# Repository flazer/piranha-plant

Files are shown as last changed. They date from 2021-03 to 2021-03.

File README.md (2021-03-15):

# Remote controlled "Mario piranha plant"

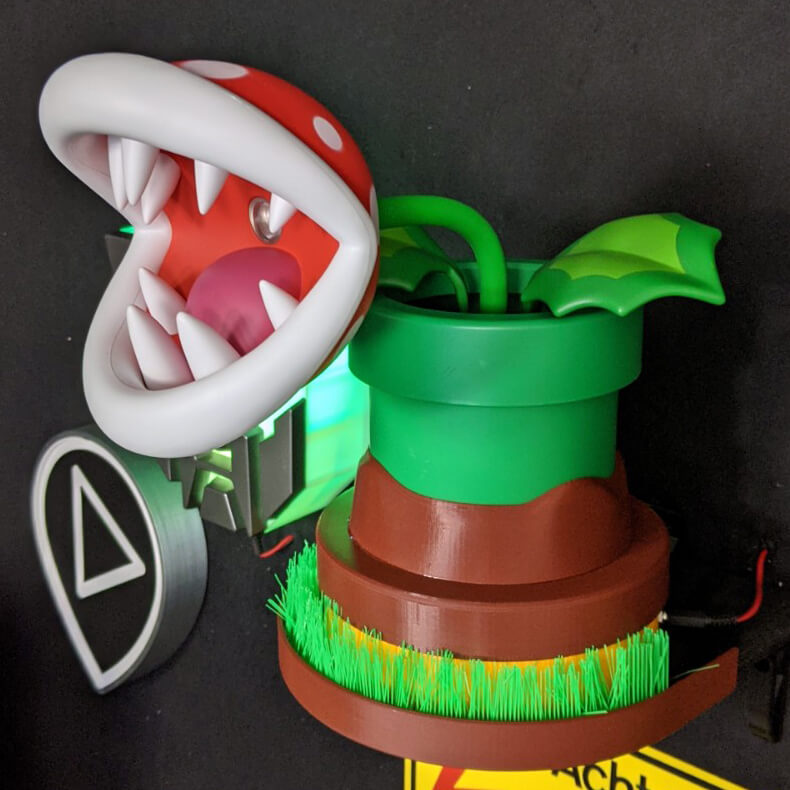
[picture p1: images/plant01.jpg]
Mario piranha plant


## Introduction
This project was realized while streaming live at [https://www.twitch.tv/chrisfigge](https://www.twitch.tv/chrisfigge).
I got this piranha plant as a christmas-gift but I think it's much cooler to use it as a remote controlled gadget while streaming.
So I wrote a lot of code, printed a lot of stuff and did this electronic-thingie.
But this time with a lot of help from the mighty community.
[0FR0](https://github.com/0FR0) tried to teach me KiCad and developed my first PCB ever.
Many, many thanks, dude! Awesome job!

So you'll find everything you need to build your own remote controlled plant in here:

- BOM (everything you've to buy)
- STL files (everything to print)
- images (everything you need to watch)
- code (everything to controll your plant via wifi)
- schematics (everything to build your own circuit)

## BOM
- 1x Wemos D1 mini: [https://amzn.to/389YZPE](https://amzn.to/389YZPE) *
- 1x Nema17 Pancake: [https://amzn.to/3bYEyGN](https://amzn.to/3bYEyGN) *
- 2x 10kOhm Resistors: [https://amzn.to/3sRnLwe](https://amzn.to/3sRnLwe) *
- 1x TMC2208 (Stepperdriver): [https://amzn.to/2PzTYd1](https://amzn.to/2PzTYd1) *
- 1x IRFZ44N (Mosfet): [https://amzn.to/3kILgEA](https://amzn.to/3kILgEA) *
- 1x LM2596 (Stepdown module): [https://amzn.to/38aoLn4](https://amzn.to/38aoLn4) *
- 1x Microswitch [https://amzn.to/3rUtHEC](https://amzn.to/3rUtHEC) *
- 1x DC-Plug [https://amzn.to/3rSaIKy](https://amzn.to/3rSaIKy) *

Links marked with an asterisk (*) are affiliates. This means if you order these items via amazon, i'll get a very small piece of this (financial) cake. You'll not pay more (not even 1 cent. literally nothing). And I can reinvest the money for new ideas and projects. From the community for the community. :)

## PCB
The pcb shown in "images" are an old previous version and differs from the current state. But works exactly the same.

## Enclosure  
If you want to print the case I've used please take a look into the "stls"-folder.  
The files are named as what they are used for.
To get a better understanding, please watch the images, stored in the "images"-folder.

## Assembly
To assemble the 3d printed parts. You will need some glue, to glue the inlay parts.
Because I'm not very good in get parts in correct position, I've printed a centering guide.
Just place the guide onto the platform and glue the "hill" nearly perfectly centered onto the baseplate. Remove the guide afterwards.

## Twitch

If you are interested in what I'm doing, just have a look at twitch:
[https://www.twitch.tv/chrisfigge](https://www.twitch.tv/chrisfigge)

## Tip
I am doing all this stuff in my freetime. And, oh boy, these projects take a lot of time. I swear.
If you want to support my work feel free to cheer some bits or giftsubs on my [Twitch channel](https://www.twitch.tv/chrisfigge) or you can always leave some tip via [paypal](https://paypal.me/flazer). Thanks a lot!

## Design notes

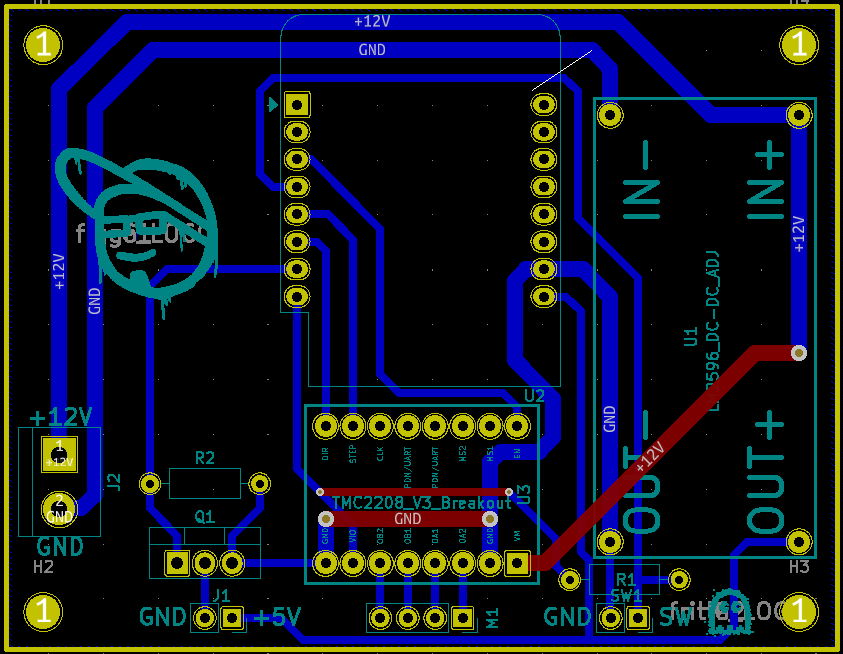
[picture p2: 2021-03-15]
schematics/layout.png

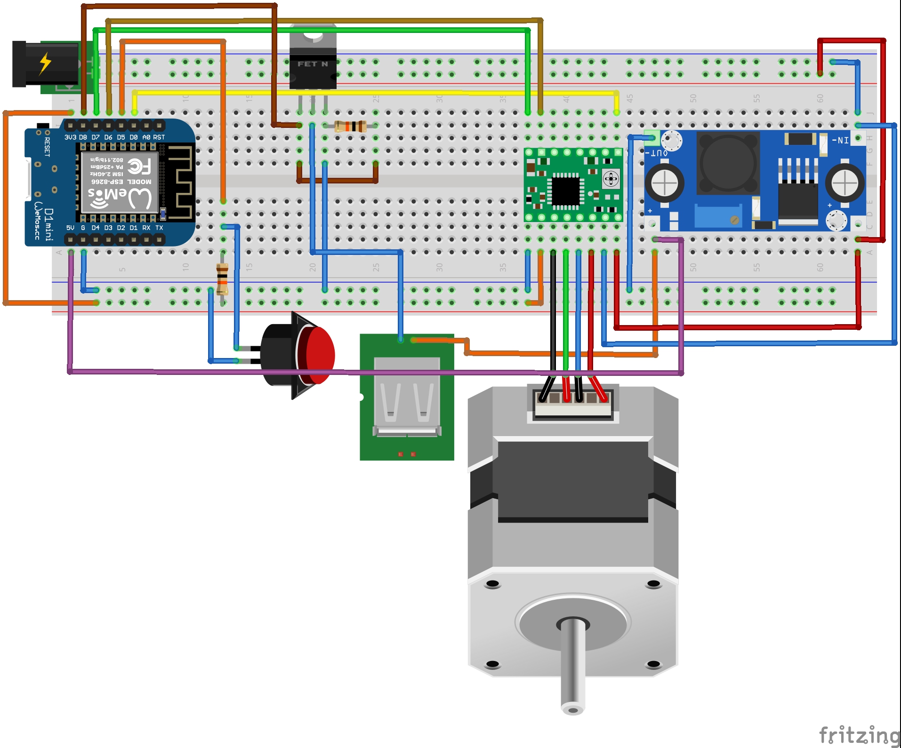
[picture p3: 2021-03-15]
schematics/fritzing/piranha-plant_Steckplatine.jpg

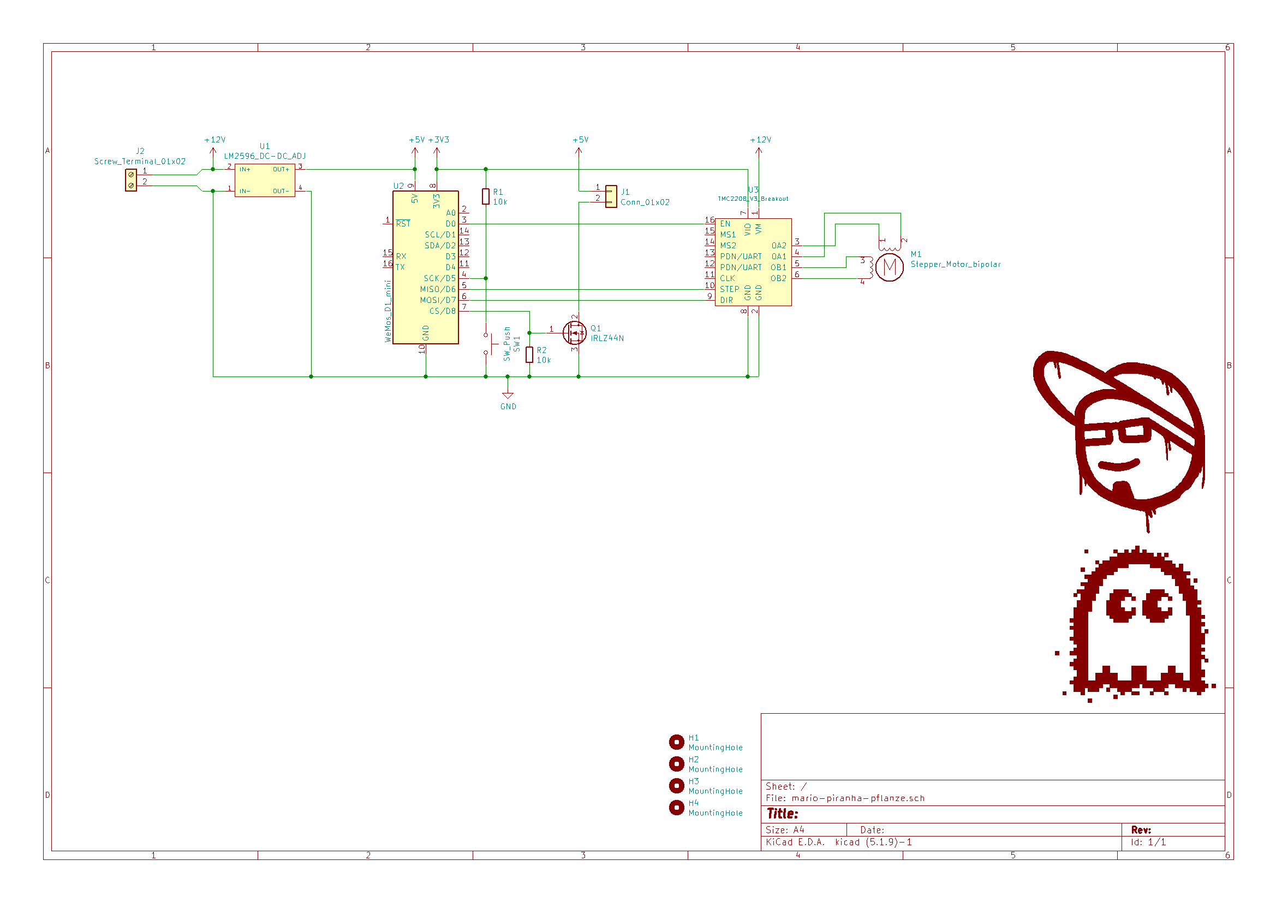
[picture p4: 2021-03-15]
schematics/scheme.png

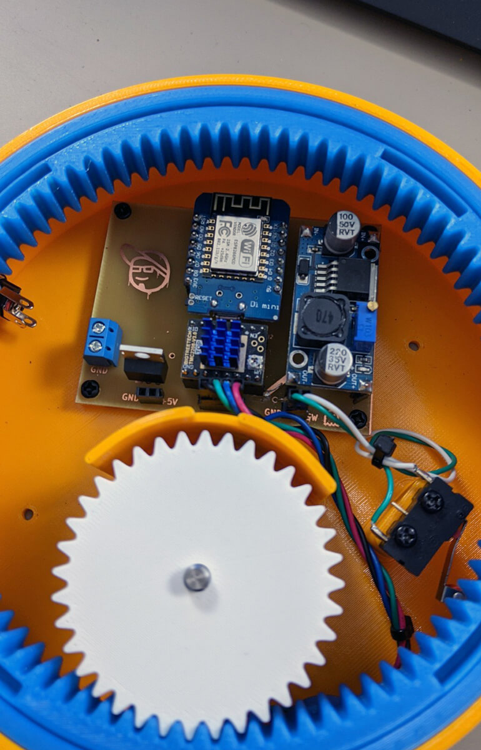
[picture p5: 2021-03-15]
images/plant05.jpg

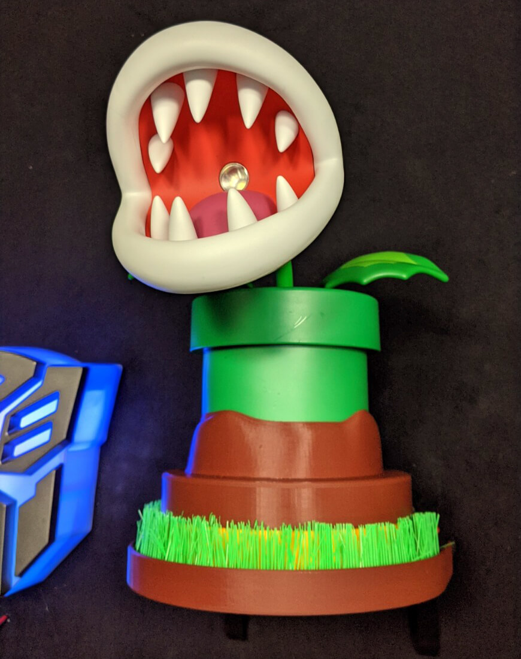
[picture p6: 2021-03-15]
images/plant02.jpg

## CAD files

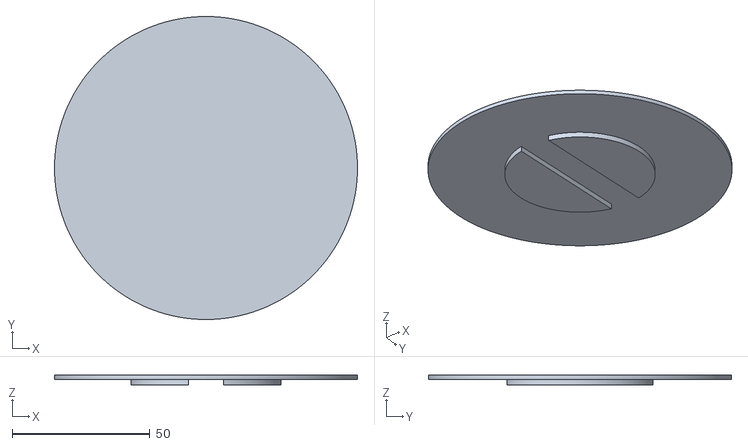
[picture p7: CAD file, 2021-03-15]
print/stl/centering-guide.stl
110.0 x 110.0 x 3.50

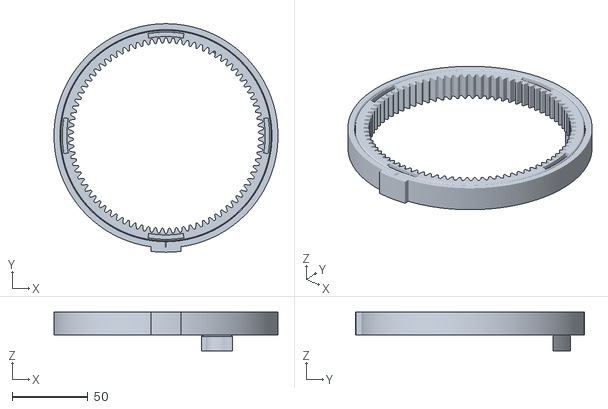
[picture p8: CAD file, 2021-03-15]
print/stl/gearring-84.stl
148.0 x 151.0 x 25.5

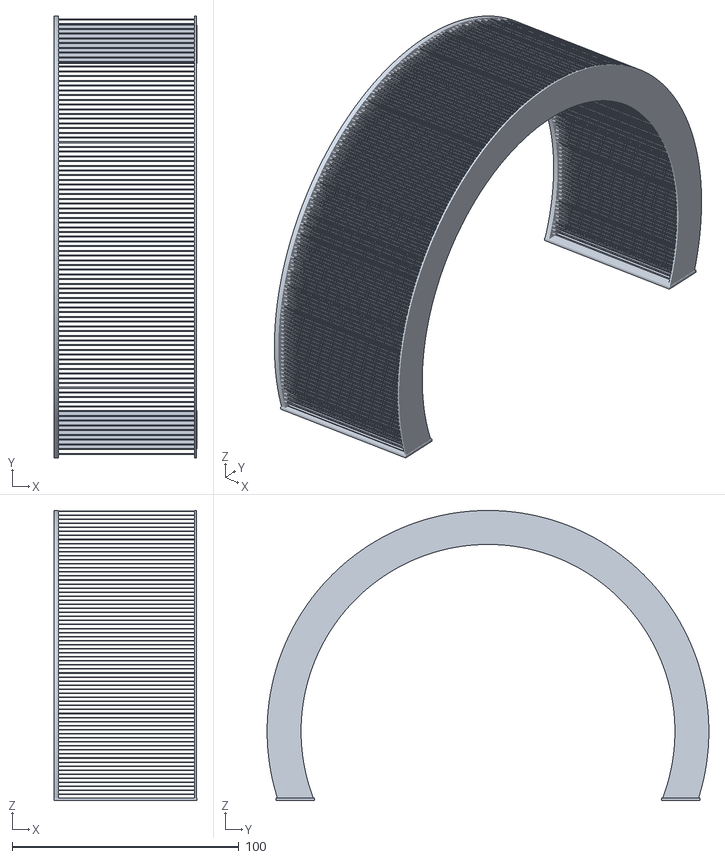
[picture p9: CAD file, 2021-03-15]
print/stl/grass.stl
63.0 x 195.0 x 128.0

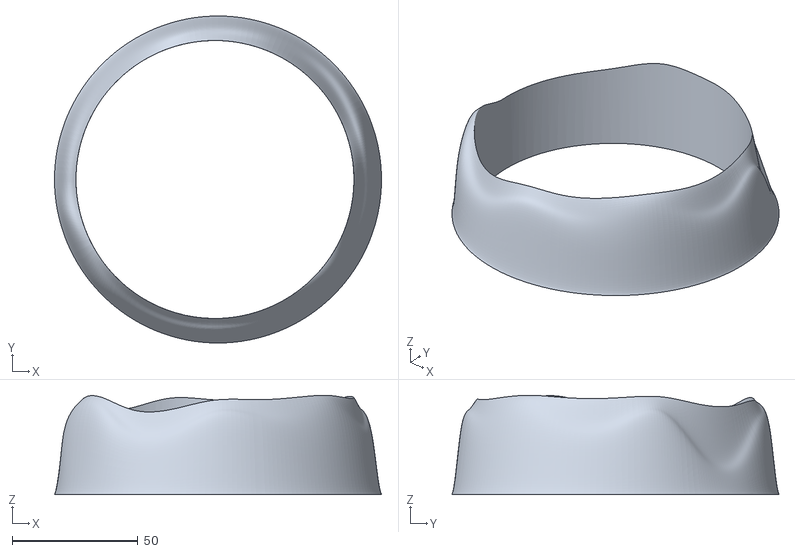
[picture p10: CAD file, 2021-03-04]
print/stl/hill.stl
130.0 x 130.0 x 39.5

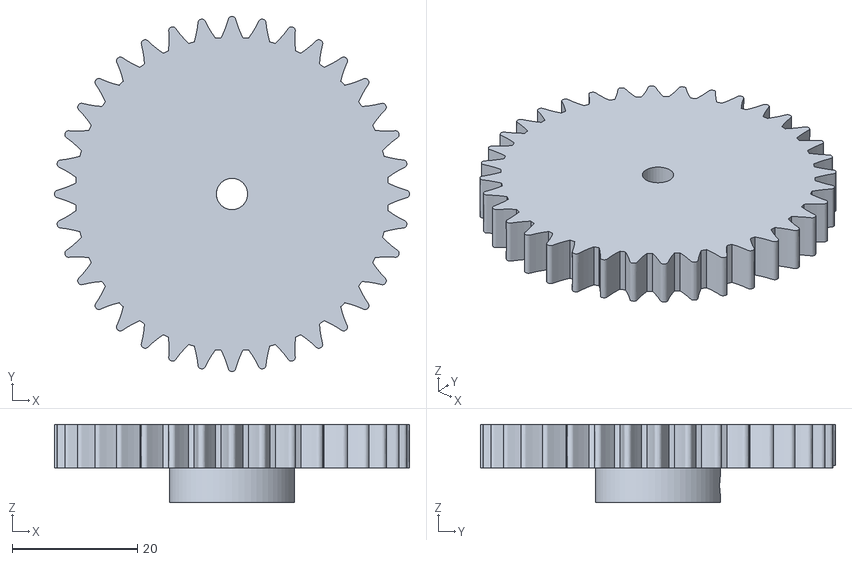
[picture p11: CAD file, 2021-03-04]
print/stl/gear-36.stl
56.7 x 56.7 x 12.5

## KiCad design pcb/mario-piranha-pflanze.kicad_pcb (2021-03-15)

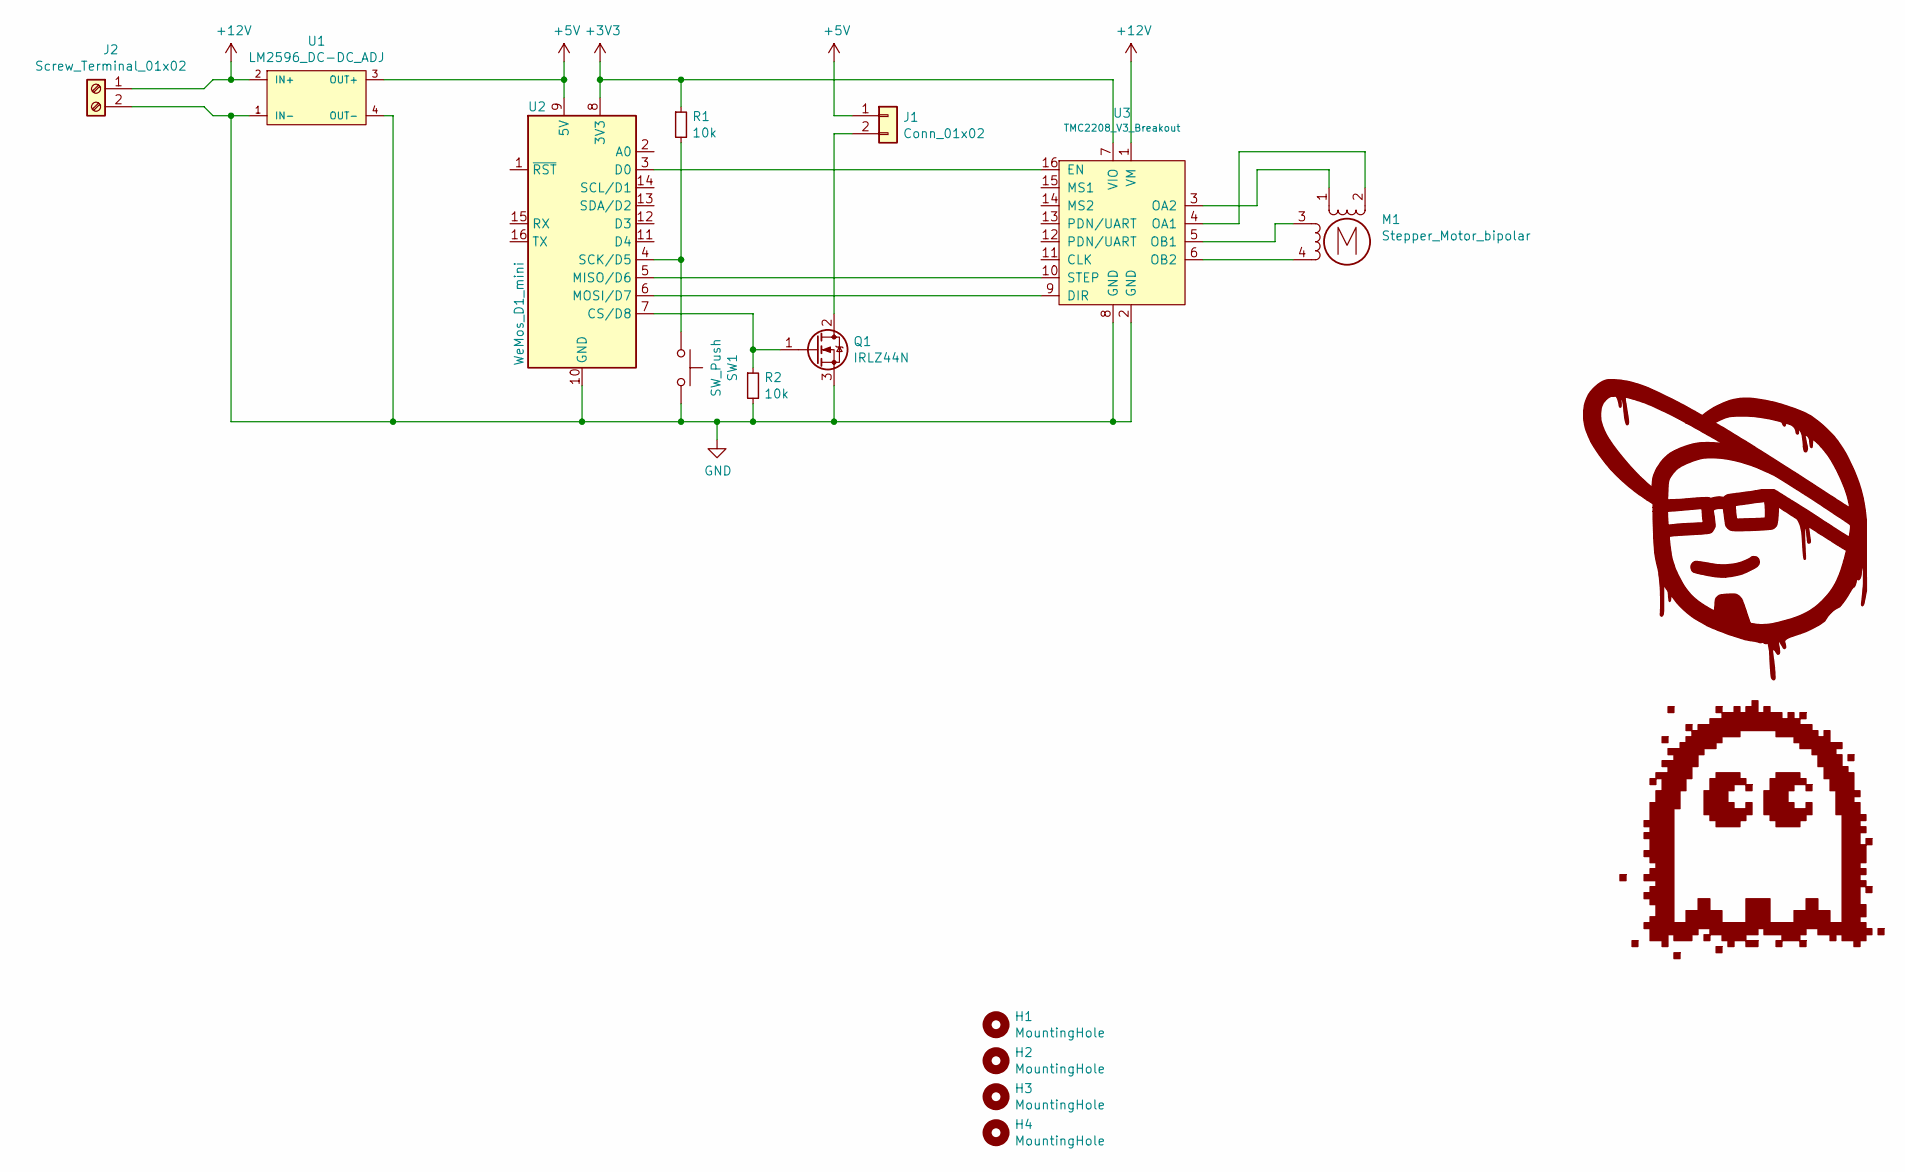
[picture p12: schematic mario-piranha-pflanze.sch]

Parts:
G1: figge_LOGO; figge_logo_15x15,9
G2: fritte_LOGO; fritte_LOGO_5x5
H1, H2, H3, H4: MountingHole; MountingHole_3.2mm_M3
J1: Conn_01x02; PinSocket_1x02_P2.54mm_Vertical
J2: Screw_Terminal_01x02; TerminalBlock_bornier-2_P5.08mm
M1: Stepper_Motor_bipolar; PinSocket_1x04_P2.54mm_Vertical
Q1: IRLZ44N; TO-220-3_Vertical
R1, R2: 10k; R_Axial_DIN0207_L6.3mm_D2.5mm_P10.16mm_Horizontal
SW1: SW_Push; PinSocket_1x02_P2.54mm_Vertical
U1: LM2596_DC-DC_ADJ; LM2596_DC-DC
U2: WeMos_D1_mini; WEMOS_D1_mini_light
U3: TMC2208_V3_Breakout

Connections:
+3V3: R1.1, U2.8 (3V3), U3.7 (VIO)
+5V: J1.1, U1.3 (OUT+), U2.9 (5V)
+12V: J2.1, U1.2 (IN+), U3.1 (VM)
GND: J2.2, Q1.3 (S), R2.2, SW1.2, U1.1 (IN-), U1.4 (OUT-), U2.10 (GND), U3.2 (GND), U3.8 (GND)
unnamed: J1.2, Q1.2 (D)
unnamed: M1.1, U3.3 (OA2)
unnamed: M1.2 (-), U3.4 (OA1)
unnamed: M1.3, U3.5 (OB1)
unnamed: M1.4, U3.6 (OB2)
unnamed: Q1.1 (G), R2.1, U2.7 (CS/D8)
unnamed: R1.2, SW1.1, U2.4 (SCK/D5)
unnamed: U2.3 (D0), U3.16 (EN)
unnamed: U2.5 (MISO/D6), U3.10 (STEP)
unnamed: U2.6 (MOSI/D7), U3.9 (DIR)

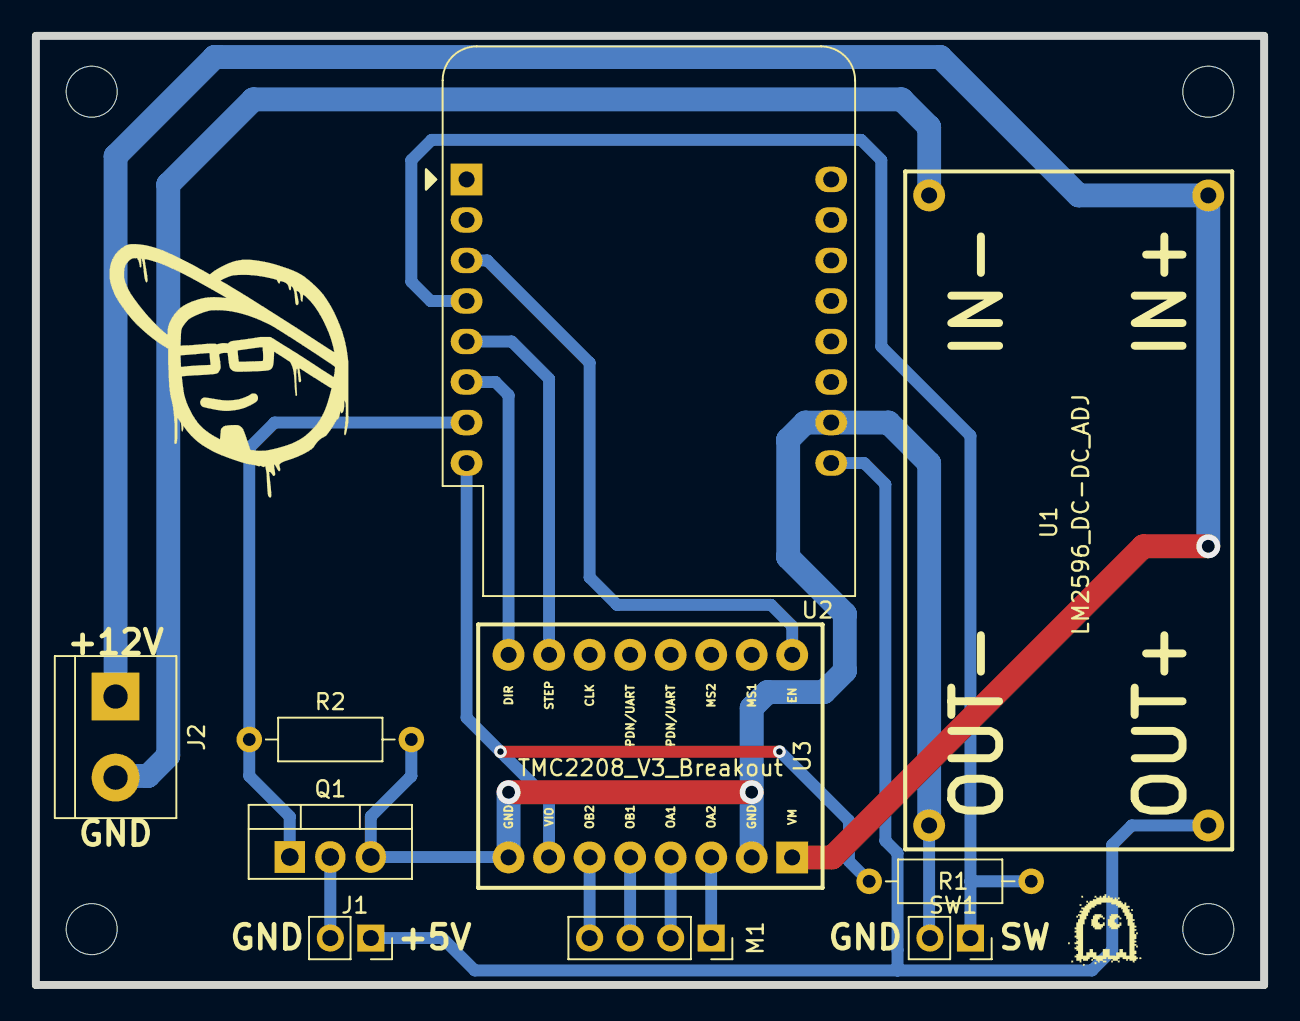
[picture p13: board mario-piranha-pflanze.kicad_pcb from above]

Board: 2 copper layers, 77.0 x 59.5 mm, 16 parts (0 on the bottom side), 14 nets.

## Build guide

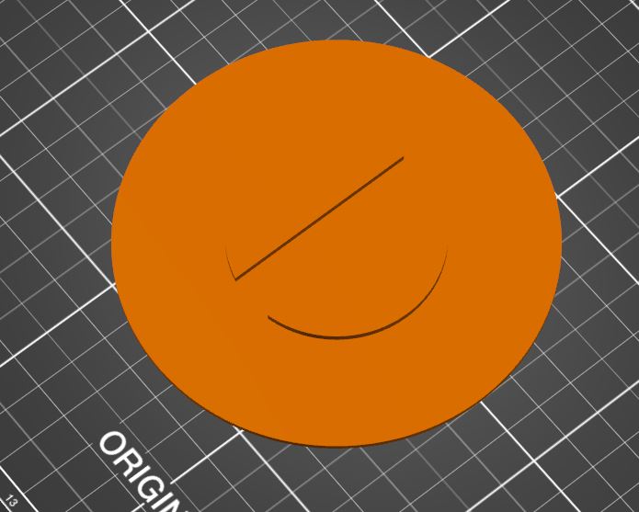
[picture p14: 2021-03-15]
print/images/centering-guide.JPG

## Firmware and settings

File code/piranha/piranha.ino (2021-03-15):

#include <ESP8266WiFi.h>
#include <ESP8266WiFiMulti.h>
#include <ESP8266HTTPClient.h>
#include <ESP8266WebServer.h>
#include <ESP8266mDNS.h>
#include <ESP8266Ping.h> //https://github.com/dancol90/ESP8266Ping
#include <Ticker.h>
#include <AccelStepper.h> //http://www.airspayce.com/mikem/arduino/AccelStepper/

#include "credentials.h"
#include "settings.h"
#include "OTA.h"

ESP8266WiFiMulti  WiFiMulti;
ESP8266WebServer  server(80);
Ticker            ticker;
AccelStepper      stepper(AccelStepper::DRIVER, STEPPER_STEP, STEPPER_DIR);
 
void setup() {
  Serial.begin(115200);
  delay(300);

  Serial.println();
  Serial.println("Setting inputs/outputs...");
  Serial.println();
  
  pinMode(BTN, INPUT);
  pinMode(LED, OUTPUT);
  pinMode(STEPPER_STEP, OUTPUT);
  pinMode(STEPPER_DIR, OUTPUT);
  pinMode(STEPPER_ENABLE, OUTPUT);
   
  digitalWrite(STEPPER_STEP, LOW);
  digitalWrite(STEPPER_DIR, LOW);
  digitalWrite(LED, LOW);
  enableMotor(false);
  
  Serial.println();
  Serial.println("Starting ticker...");
  Serial.println();
  ticker.attach(1, loopCount);

  Serial.println();
  Serial.println("Initializing stepper...");
  Serial.println();
  stepper.setAcceleration(80);
  stepper.setMaxSpeed(maxMotorSpeed);
  
  Serial.println("");
  startWIFI();
  handleOTASetup();
  startWebserver();

  Serial.println();
  Serial.println("Homing");
  homingMode = true;
  Serial.println();
}


/**
 * Wrapper for more ease moving 
 * the motor
 */
void moveDeg(int deg) {
  // 360° = 466 * 8 = 3728 steps
  int steps = 466 * 8 / 360;
  steps = steps * deg;
  Serial.println(steps);
  stepper.move(steps);
}


/**
 * Homing the whole platform
 * Handling when state is in "homing"-mode.
 */
void homePlatform() {
  enableMotor(true);

  switch(homingModeStep) {
    case 0:
      digitalWrite(LED, HIGH);
      stepper.setSpeed(maxMotorSpeed);
      moveDeg(10);
      homingModeStep++;
      break;

    case 1:
      if(!stepper.isRunning()) {
        digitalWrite(LED, LOW);
        moveDeg(-180);
        homingModeStep++;
      }
      break;

    case 2:
      if(!digitalRead(BTN)) {
        stepper.setAcceleration(avgAccSpeed * 2);
        stepper.stop();
        homingModeStep++;
      }
      break;

    case 3:
      if(!stepper.isRunning()) {
        stepper.setAcceleration(avgAccSpeed);
        digitalWrite(LED, HIGH);
        moveDeg(60);
        homingModeStep++;
      }
    break;

    case 4:
      if(!stepper.isRunning()) {
        digitalWrite(LED, LOW);
        stepper.disableOutputs();
        enableMotor(false);
        homingModeStep = 99;
        homingMode = false;
        Serial.println("Successfully homed!");
      }
    break;
  }
}


/**
 * Playing moving pattern
 * Handling when state is in "patternActive"-mode.
 */
void playPattern() {
  enableMotor(true);

  switch(patternStep) {
    case 0:
      moveDeg(60);
      patternStep++;
      break;

    case 1:
      if(!stepper.isRunning()) {
        moveDeg(-125);
        patternStep++;
      }
      break;

    case 2:
      if(!digitalRead(BTN)) {
        stepper.setAcceleration(avgAccSpeed * 2);
        stepper.stop();
        patternStep++;
      }
      break;

    case 3:
      if(!stepper.isRunning()) {
        stepper.setAcceleration(avgAccSpeed);
        moveDeg(120);
        if(patternLoop < patternRepeats) {
          patternLoop++;
          patternStep = 1;
        } else {
          patternStep++;
        }
      }
    break;

  case 4:
    if(!stepper.isRunning()) {
      moveDeg(-60);
      patternStep++;
    }
    break;

    case 5:
      if(!stepper.isRunning()) {
        stepper.disableOutputs();
        enableMotor(false);
        patternStep = 0;
        patternLoop = 0;
        patternLed = 0;
        ledActive = false;
        digitalWrite(LED, ledActive);
        patternActive = false;
        Serial.println("Successfully end pattern!");
      }
    break;
  }
}


/**
 * Switching led on/off if x ms passed
 */
void handleLed() {
  if(patternLed > 0 && lastHitMillis < millis() && millis() % 1000 == 0) {
    lastHitMillis = millis();
    ledActive = !ledActive;
    digitalWrite(LED, ledActive);
  }
}


/**
   Handles pinging (send alive)
   to server
*/
void handlePing() {
  if (pingCnt > handlePingSecs) {
    Serial.println("Start pinging.");
    bool result = Ping.ping("www.google.com");

    if (!result) {
      Serial.println("Ping failed!");
    }

    Serial.println("[HTTP] end ping-pong.");
    Serial.println("---");
    pingCnt = 0;
  }
}


/**
 * Preparing movePattern by parsing and setting 
 * all params given by request
 */
void startMovePattern(uint8_t speed, uint8_t repeats, uint8_t led) {
  server.send(200, "text/plain", "Start movement.");
  patternActive = true;

  patternSpeed = patternSpeedFallback;
  if(speed > 0) patternSpeed = speed;
  if(speed > maxMotorSpeed) patternSpeed = maxMotorSpeed;

  patternRepeats = patternRepeatsFallback;
  if(repeats > 0) patternRepeats = repeats;
  
  patternLed = patternLedFallback;
  if(led > 0) patternLed = led;
  
  Serial.println("Start da movement");
}


/**
   Start webserver for handling
   incoming requests
*/
void startWebserver() {
  Serial.println("Starting HTTP-Server...");
  Serial.println("-- Registering routes.");
  server.on("/pattern", HTTP_GET, []() {
    String speed = server.arg("speed");
    String repeats = server.arg("repeats");
    String led = server.arg("led");
    startMovePattern(speed.toInt(), repeats.toInt(), led.toInt());
  });
  server.onNotFound(handleRequestNotFound);
  Serial.println("-- Launching server ...");
  server.begin();
  Serial.println("-- DONE.");
}


/**
   Start or reconnect the wifi
   by switching into an infinite loop
   as long as the connection is broken
*/
void startWIFI() {
  int loopcnt = 0;
  Serial.println("---");
  WiFi.mode(WIFI_STA);
  Serial.println("Connecting WIFI.");
  Serial.println("(Re)Connecting to Wifi-Network with following credentials:");
  Serial.print("SSID: ");
  //Serial.println(WifiCredentials[0].c_str());
  Serial.print("Key: ");
  //Serial.println(WifiCredentials[1].c_str());
  WiFi.hostname(espName);
  WiFiMulti.addAP(WifiCredentials[0].c_str(), WifiCredentials[1].c_str());

  while (WiFiMulti.run() != WL_CONNECTED) {
    loopcnt++;
    if(loopcnt < 10) {
      Serial.print(".");
    }
    delay(500);
  }

  Serial.println("");
  Serial.println("WiFi connected.");
  Serial.println("IP address:");
  Serial.println(WiFi.localIP().toString());
}


/**
   Tick, tick, tick
*/
void loopCount() {
  loopCnt++;
  pingCnt++;
}


/**
 * DA MAINLOOP
 */
void loop() {
   //(re)connect wifi if not connected
  if (WiFiMulti.run() != WL_CONNECTED) {
    delay(1);
    startWIFI();
    return;
  }

  stepper.run();

  if(homingMode) {
    homePlatform();
    return;  
  }

  if(patternActive) {
    playPattern();
    handleLed();
    return;
  }

  if(stepper.isRunning()) {
    return;
  }
  
  ArduinoOTA.handle();
  handlePing();
  server.handleClient();
   
}


/**
 * Wrapper for handling the motor more 
 * intuitively
 */
void enableMotor(boolean enable) {
  digitalWrite(STEPPER_ENABLE, !enable);
}


/**
   Unknown Route
   Send "teapot".
*/
void handleRequestNotFound() {
  server.send(418, "text/plain", "I'm a piranha-plant. Chhhrrapppp! Chhhrrapppp!");
}

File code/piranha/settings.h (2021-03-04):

#define BTN             D5 //Button
#define LED             D8 //LED
#define STEPPER_STEP    D6 //Step
#define STEPPER_DIR     D7 //Direction
#define STEPPER_ENABLE  D0 //Enable 

//Interval to ping server in seconds (to avoid losing wifi)
int handlePingSecs = 120;

int maxMotorSpeed = 500; //Maximum speed of motor
int avgAccSpeed   = 900; //Normal acceleration speed 

boolean patternLedFallback = 0; //Fallback if no led-option was send via request
uint8_t patternRepeatsFallback = 3; //Fallback if no repeat-option was send via request
uint8_t patternSpeedFallback = 500; //Fallback if no speed-option was send via request

//Hostname of your esp
const char* espName = "esp8266-studio-piranha-plant"; 

//Internal settings. 
//Don't change anything below (except you really know what you're doing).

int loopCnt = 0;
int pingCnt = 0;

boolean homingMode = false;
int homingModeStep = 0;

bool ledActive     = false;
bool patternActive = false;
int patternRepeats = 0;
int patternSpeed   = 0;
int patternLed     = 0;
int patternStep    = 0;
int patternLoop    = 0;
int lastHitMillis  = 0;
